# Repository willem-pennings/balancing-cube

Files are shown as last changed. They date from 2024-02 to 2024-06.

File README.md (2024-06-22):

## Balancing cube

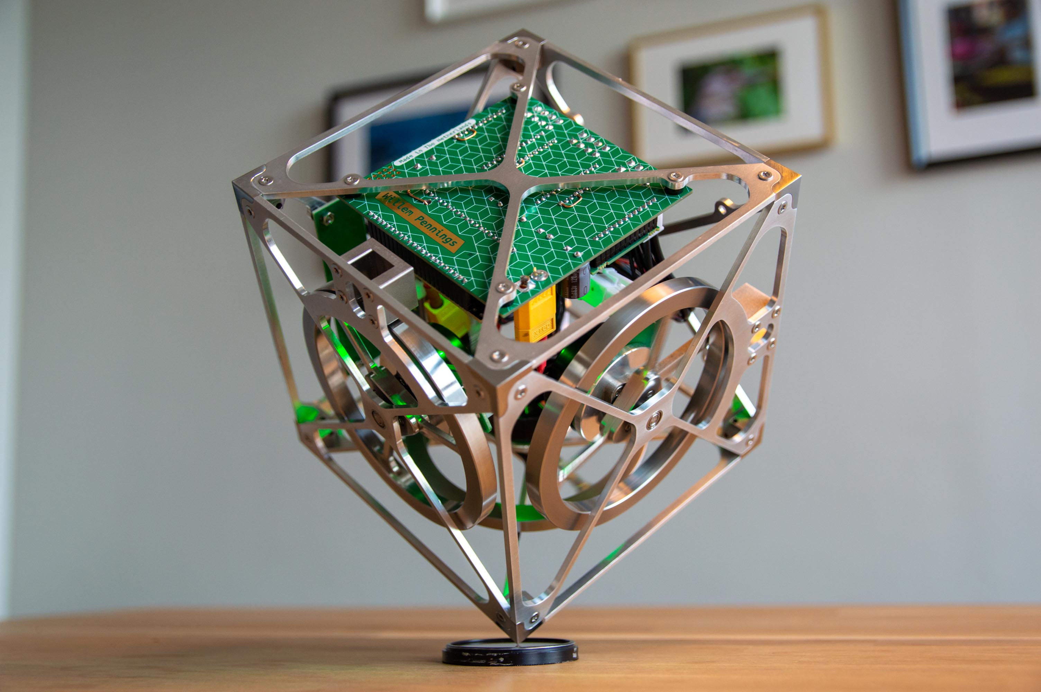
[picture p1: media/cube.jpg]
The cube balances on its corner using three integrated reaction wheels


This repository contains all design, documentation, configuration and other files related to the balancing cube that I have designed and built.
* Mechanical parts are designed in [Fusion 360](https://www.autodesk.com/products/fusion-360/personal).
* Circuit boards are designed in [KiCad 7](https://www.kicad.org/download/windows/).
* Code has been written using [Arduino IDE](https://docs.arduino.cc/software/ide-v2/tutorials/getting-started/ide-v2-downloading-and-installing/).
* Motor drivers are commissioned and tuned using [Escon Studio](https://www.maxongroup.nl/maxon/view/content/ESCON-Detailsite?isoCode=nl).
* Motors and motor controllers are available from [Maxon](https://www.maxongroup.com/maxon/view/content/index).
* Circuit boards and custom mechanical parts can be ordered from [PCBWay](https://www.pcbway.com/rapid-prototyping/), for example.

A YouTube video demonstrating the balancing cube is available [here](https://youtu.be/zGclFqkZBsk).

### Want to build one? Read this!

This repository should contain everything you need to order and/or build parts for this cube. Take into account the following:

* I replaced four of the eight 16AWG wires in each cable assembly by 22AWG wires since only four wires carry large currents. The others carry +5V and hall sensor signals. This reduces weight and makes the cables easier to handle, as well as reducing strain on the mating connectors. The motor connection is rather fragile and might break if stressed too much.
* The ESP32 board does not go into flashing mode automatically. I fixed this by adding a 10 uF capacitor between the enable and reset pin, as described [here](https://randomnerdtutorials.com/solved-failed-to-connect-to-esp32-timed-out-waiting-for-packet-header/).
* In my blog post, I describe some errors in the design of the motherboard. These have been resolved in the files that are available in this repository.
* For your own safety, I highly recommend taking precautions to reduce the risk of trapping fingers between the spinning flywheels. One option is to attach very thin (spring steel) discs to each wheel, which may be (laser)cut from larger sheets that are readily available. I do not have designs available for such safety devices yet.

### More information

More information about this project and my other projects is available on my [website](https://willempennings.nl/balancing-cube/).

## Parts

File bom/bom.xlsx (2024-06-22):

Quantity | Name | Designators | Part number | Supplier
3 | Aluminium Electrolytic Capacitors - Radial Leaded 120uF 63 Volts 20% | C1, C2, C3 | 647-UPM1J121MHD6TO | Mouser
1 | Aluminium Electrolytic Capacitors - Radial Leaded 50volts 470uF 18x15 20% 7.5LS | C4 | 647-UPJ1H471MHD6 | Mouser
1 | Aluminium Electrolytic Capacitors - Radial Leaded 25volts 220uF 10x12.5 '20% 5LS | C5 | 647-UPJ1E221MPD6 | Mouser
6 | Multilayer Ceramic Capacitors MLCC - SMD/SMT 50V 0.1uF X7R 0603 10% Flex AEC-Q200 | C6, C7, C8, C9, C10, C11 | 80-C0603X104K5R3316 | Mouser
2 | Multilayer Ceramic Capacitors MLCC - SMD/SMT 10V 10uF X5R 0603 20% | C12, C13 | 80-C0603C106M8PACTU | Mouser
3 | ESD Suppressors / TVS Diodes 33V 1000W UniDir TransZorb 5% Tol | D1, D2, D3 | 78-SMBJ33A | Mouser
1 | Schottky Diodes & Rectifiers 40V 3A SCHOTTKY RECTIF | D4 | 863-NRVBSS34FA | Mouser
3 | ESD Suppressors / TVS Diodes 3.3V Bidirectional | D5, D6, D7 | 652-CDDFN2-T3.3B | Mouser
3 | Surface Mount Fuses 260C 4A SMF NANO CLIP VFA | F1, F2, F3 | 576-0157004.DR | Mouser
4 | XT60 connector female |  | 474-PRT-10474 | Mouser
4 | XT60 connector male | J1 | 474-PRT-10474 | Mouser
3 | Headers & Wire Housings 8 CKT VERT HEADER | J2, J3, J4 | 538-39-28-1083 | Mouser
3 | Rectangular Cable Assemblies MINIFIT JR DR R-R 8CKT 150MM Sn |  | 538-215325-1081 | Mouser
1 | Headers & Wire Housings Classic PCB Header Strips, 0.100" pitch | J5 | 200-TSW10607LT | Mouser
1 | Power Inductors - SMD Ind,11x10x5.1mm,68uH+/-20%,3.5A,shd | L1 | 652-SRP1050WA-680M | Mouser
2 | MOSFET 50V, 0.26A, Single N-Channel Power MOSFET | Q1, Q2 | 821-BSS138 | Mouser
4 | Thick Film Resistors - SMD 10K OHM 5% | R1, R2, R3, R4 | 71-RCA060310K0JNEA | Mouser
1 | WiFi Development Tools - 802.11 ESP32-S3 Gen-Purpose Dev Bd, ESP32-S3-WROOM-1 | U4 | 356-EP32S3DVKTC1N8R8 | Mouser
1 | Switching Voltage Regulators 150 KHZ 3A STEP-DOWN VLTG REG | U5 | 926-LM2596SX-5.0NOPB | Mouser
1 | LDO Voltage Regulators High Vin, Low Iq Regulator | U6 | 998-MIC5225-1.8YM5TR | Mouser
1 | IMUs - Inertial Measurement Units World's Lowest Power 9-Axis MEMS MotionTracking | U7 | 410-ICM-20948 | Mouser
7 | Headers & Wire Housings |  | 801-87-011-10-005101 | Mouser
3 | Headers & Wire Housings |  | 801-87-013-10-005101 | Mouser
2 | Slide Switches Slide DPST | SW1, SW2 | 611-L201011MS02Q | Mouser
3 | EC 45 flat ∅42.8 mm, brushless, 60 W, with Hall sensors | Open rotor |  | 591477 | Maxon
3 | ESCON Module 24/2, 4-Q servo controller for DC/EC motors, 2/6 A, 10-24 VDC |  | 466023 | Maxon
3 | Machined part: motor frame (aluminium 6061)
3 | Machined part: regular frame (aluminium 6061)
3 | Machined part: bridge (stainless steel 304)
3 | Machined part: hub (stainless steel 304)
3 | Machined part: wheel (stainless steel 304)
4 | Machined part: Cornerstone A/CW (stainless steel 304)
4 | Machined part: Cornerstone B/CCW (stainless steel 304)
1 | Tattu Funfly Series 1300mAh 22.2V 100C 6S1P LiPo
1 | Custom PCB: cube-motherboard (4-layer ENIG)
1 | Custom PCB: cube-batteryboard (2-layer HASL)
9 | Machine screw M3x6 countersunk (motor - bridge)
8 | Machine screw M3x10 countersunk (frame - batteryboard, frame - motherboard)
8 | Nut M3
8 | Nylon spacer black ID 3.2 mm OD 7 mm
9 | Set screw hex M3x4 (hub - motor)
9 | Machine screw M2x6 countersunk (wheel - hub)
36 | Machine screw M3x8 countersunk (cornerstone - frame, frame - bridge)
3 | Radial ball bearing, 4 mm x 9 mm x 4 mm (bore diameter x outer diameter x width) |  | 638-4-ZZ-SKF

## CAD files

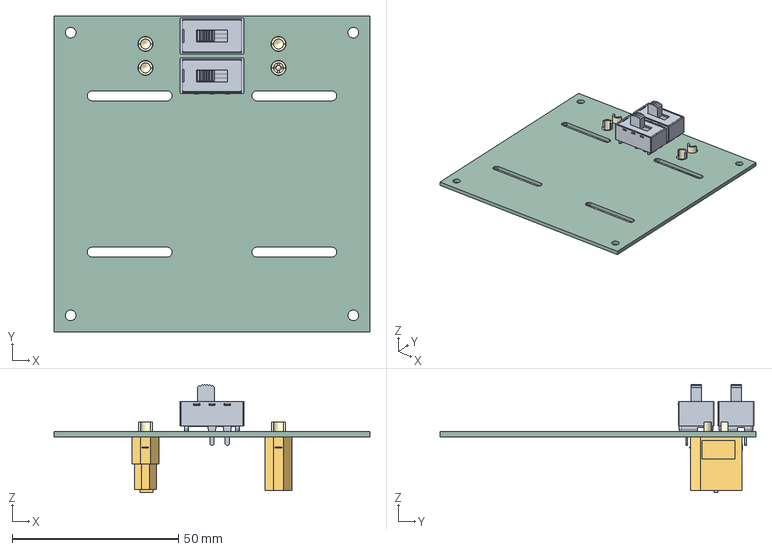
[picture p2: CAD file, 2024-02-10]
electronics/cube-batteryboard/cube-batteryboard.step
95.0 x 95.0 x 32.6 mm
Cubli batteryboard PCB

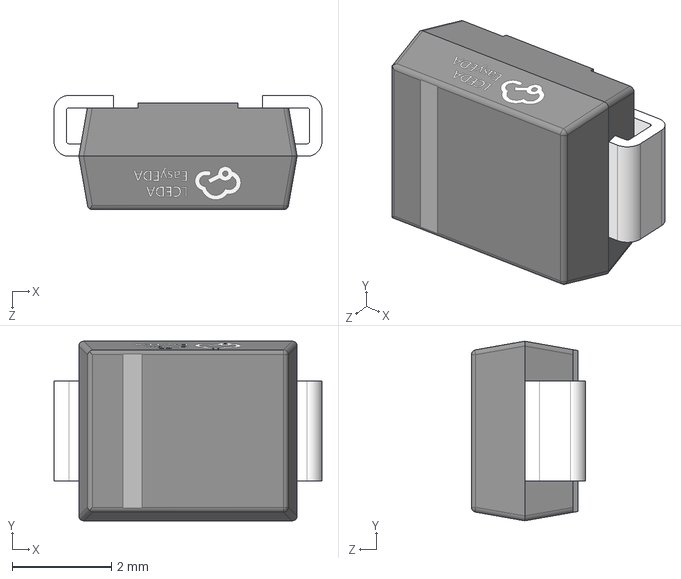
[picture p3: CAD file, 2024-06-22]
electronics/cube-motherboard/3d models/SMB_L4.4-W3.6-LS5.4-RD.step
5.40 x 3.62 x 2.30 mm

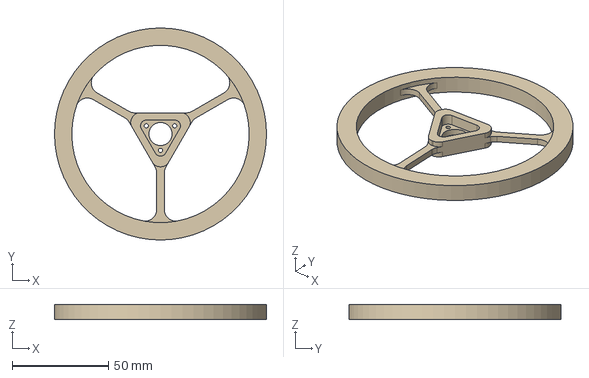
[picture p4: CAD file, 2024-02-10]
mechanical/models/wheel.step
110.0 x 110.0 x 8.00 mm

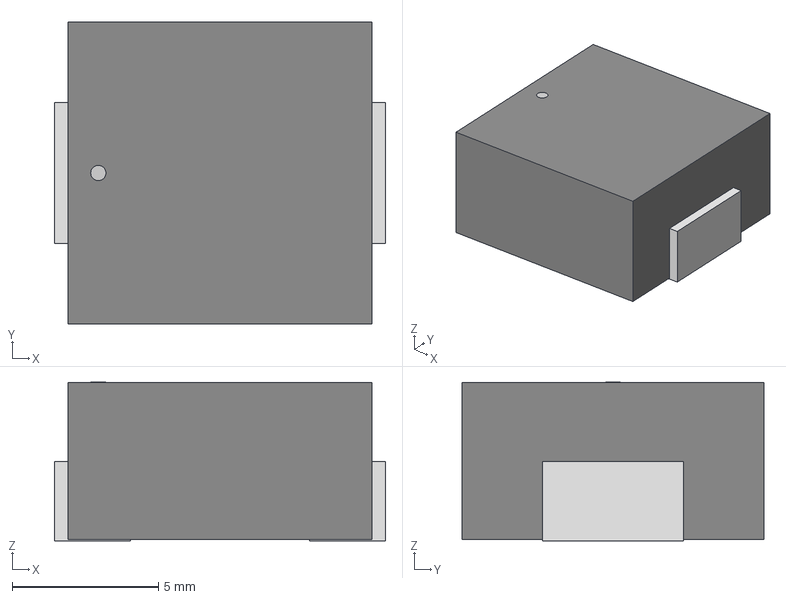
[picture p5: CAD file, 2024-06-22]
electronics/cube-motherboard/3d models/IND_SRP1050_BRN.step
11.3 x 10.3 x 5.41 mm

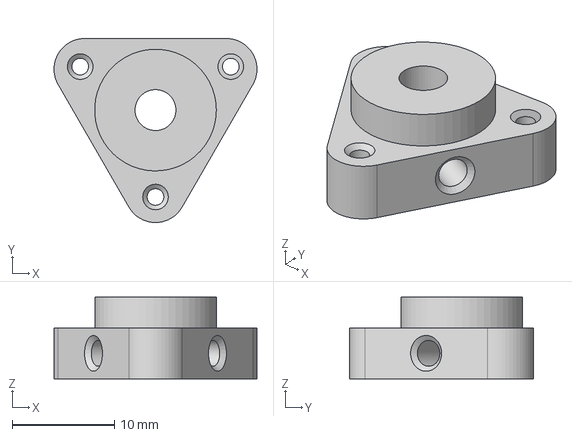
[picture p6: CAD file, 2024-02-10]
mechanical/models/hub.step
19.9 x 18.0 x 8.00 mm

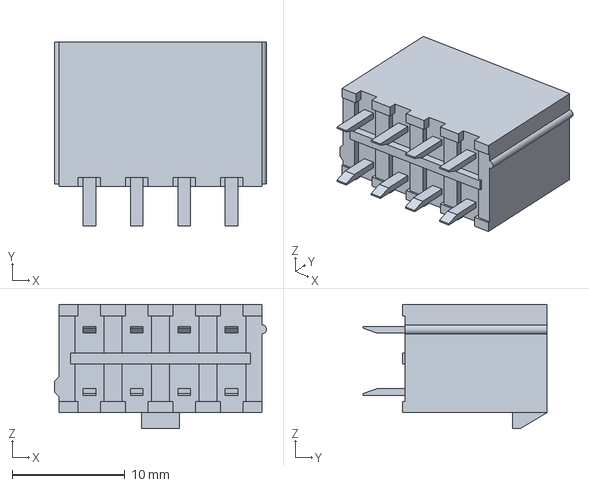
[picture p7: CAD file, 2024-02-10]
electronics/cube-motherboard/3d models/Molex 39281083.stp
18.8 x 16.3 x 11.0 mm

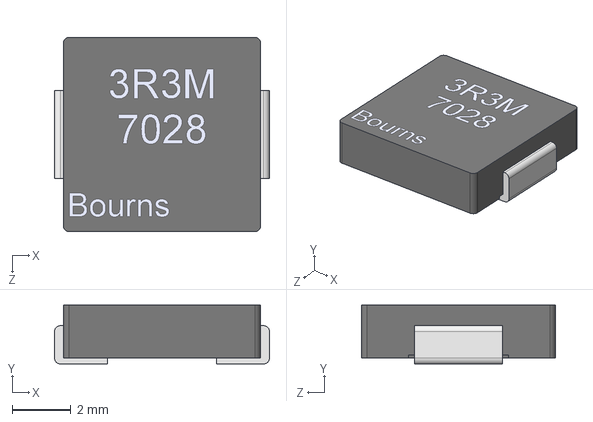
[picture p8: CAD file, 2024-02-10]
electronics/cube-motherboard/3d models/SRP7028A-3R3M.STEP
7.30 x 2.00 x 6.60 mm

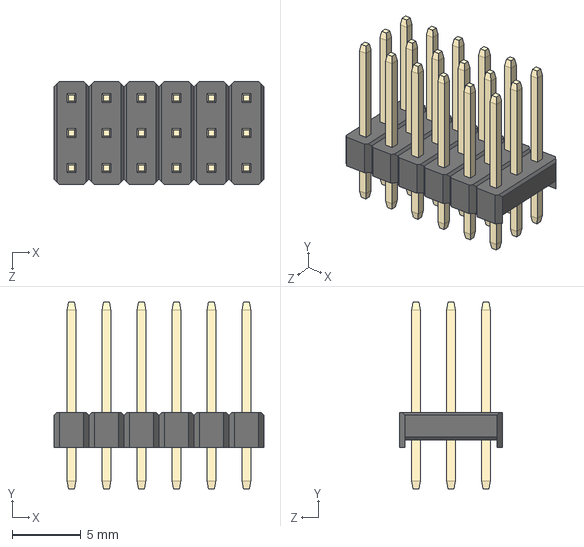
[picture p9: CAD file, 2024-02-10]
electronics/cube-motherboard/3d models/3x6 Male Pin Header.STEP
15.2 x 13.5 x 7.50 mm

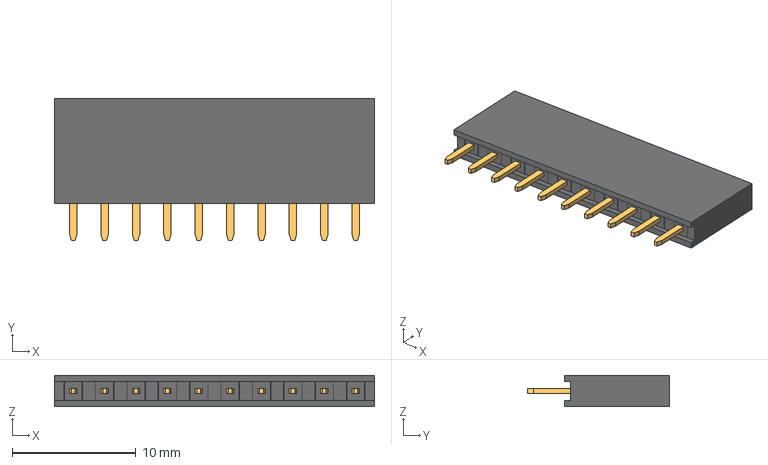
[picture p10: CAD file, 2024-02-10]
electronics/cube-motherboard/3d models/zl262-10s_p2-54_l25-9_w2-5_h8-5.stp
25.9 x 11.5 x 2.54 mm

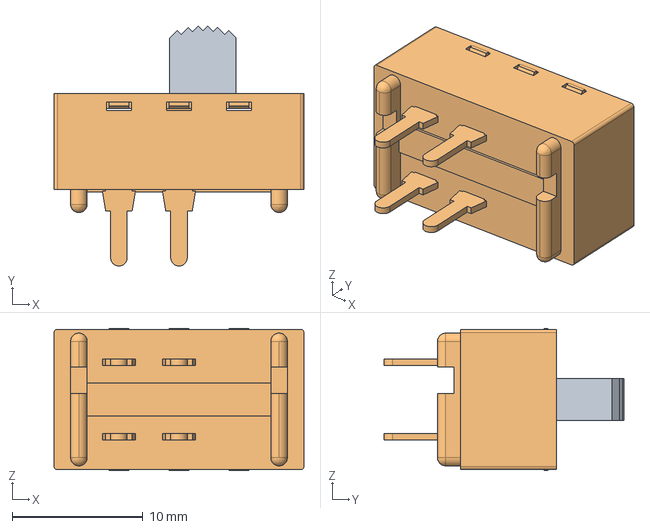
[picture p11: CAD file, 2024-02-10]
electronics/cube-batteryboard/3d models/L201011MS02Q.stp
19.1 x 18.4 x 10.9 mm

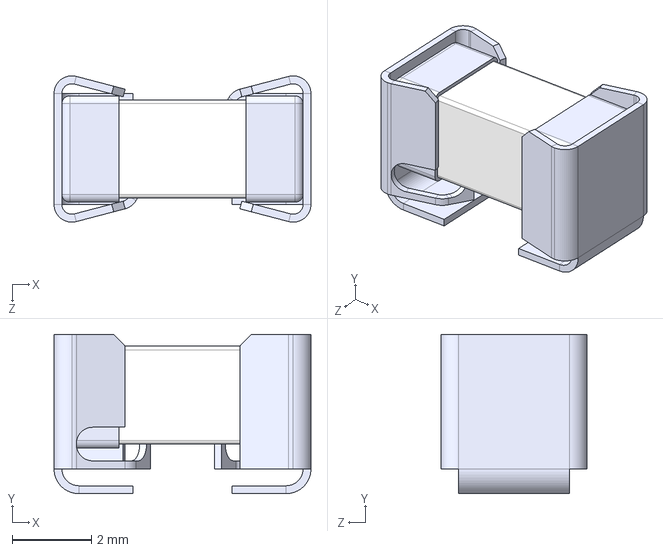
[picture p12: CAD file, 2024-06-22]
electronics/cube-motherboard/3d models/0157004.DRT.STEP
6.50 x 4.03 x 3.70 mm

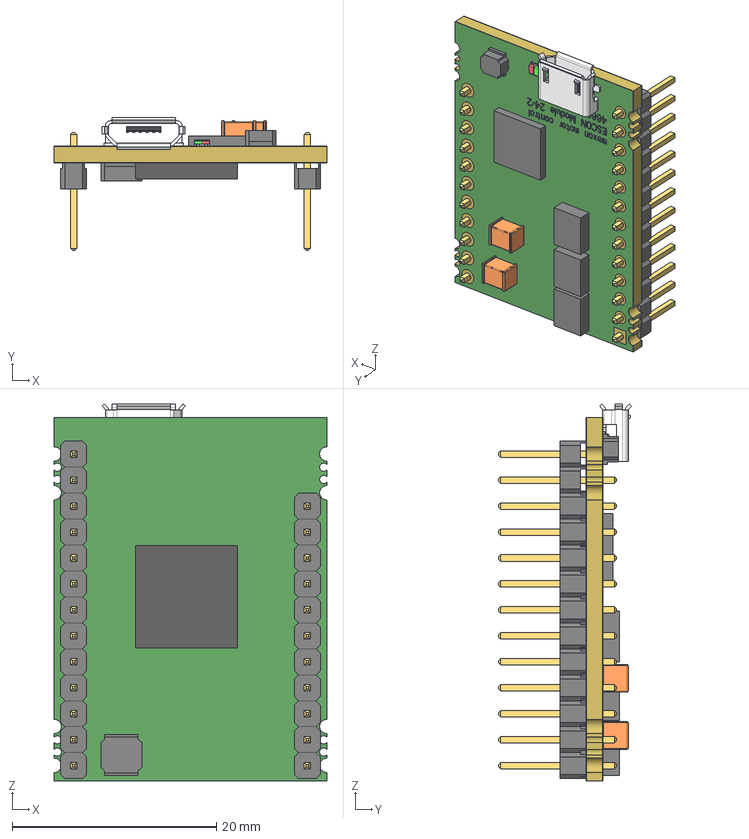
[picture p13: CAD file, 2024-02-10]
electronics/cube-motherboard/3d models/466023_escon_module_24-2.stp
26.7 x 13.0 x 36.9 mm
ESCON_24-2_MODULE_PCB
CAP_C3225 x 2
USB_MICRO
IC_7X7X1
DROSSEL_4X4X1-8
IC_LQFP64-10X10
ESCON_24-2_MODULE_PCB_SI-T
ESCON_24-2_MODULE_PCB_SI-B
STIFTLEISTE_1X1_K x 24
STIFTLEISTE_STIFT x 24
LED-0606_DUAL_SOCKEL
LED-0606-DUAL_GRUEN
LED-0606-DUAL_ROT
IC_SO-08 x 3
DROSSEL_3X3X1-5

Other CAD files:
mechanical/models/bridge.f3d
mechanical/models/cornerstone-a.f3d
mechanical/models/cornerstone-b.f3d
mechanical/models/frame-motor.f3d
mechanical/models/frame-regular.f3d
mechanical/models/hub.f3d
mechanical/models/mount-brake.f3d
mechanical/models/wheel.f3d

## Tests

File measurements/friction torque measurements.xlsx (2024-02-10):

Current (A) | Torque (Nm) | Speed (rpm) | Speed (rad/s) | Remark
0.050 | 0.00180 | 0.00 | 0.00
0.100 | 0.00360 | 0.00 | 0.00
0.110 | 0.00396 | 0.00 | 0.00
0.120 | 0.00432 | 0.00 | 0.00
0.130 | 0.00468 | 0.00 | 0.00
0.140 | 0.00504 | 1029.00 | 107.76 | Static friction overcome
0.150 | 0.00540 | 1227.00 | 128.49
0.160 | 0.00576 | 1476.00 | 154.57
0.170 | 0.00612 | 1687.00 | 176.66
0.180 | 0.00648 | 1890.00 | 197.92
0.190 | 0.00684 | 2130.00 | 223.05
0.200 | 0.00720 | 2380.00 | 249.23
0.210 | 0.00756 | 2640.00 | 276.46
0.220 | 0.00792 | 2852.00 | 298.66
0.230 | 0.00828 | 3109.00 | 325.57
0.240 | 0.00864 | 3349.00 | 350.71
0.250 | 0.00900 | 3597.00 | 376.68
0.260 | 0.00936 | 3819.00 | 399.92
0.270 | 0.00972 | 4032.00 | 422.23
0.280 | 0.01008 | 4260.00 | 446.11
0.290 | 0.01044 | 4475.00 | 468.62
0.300 | 0.01080 | 4639.00 | 485.79
0.310 | 0.01116 | 4896.00 | 512.71
0.320 | 0.01152 | 5102.00 | 534.28
0.330 | 0.01188 | 5345.00 | 559.73
0.340 | 0.01224 | 5618.00 | 588.32
0.350 | 0.01260 | 5830.00 | 610.52
0.360 | 0.01296 | 5890.00 | 616.80 | Output voltage saturation
0.140 | 0.00504 | 1069.00 | 111.95 | Back towards zero
0.130 | 0.00468 | 862.00 | 90.27
0.120 | 0.00432 | 650.00 | 68.07
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

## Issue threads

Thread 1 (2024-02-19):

Include parts list?

x46085, 2024-02-19:
Hello!

I've set about trying to build this, and ordered all the parts listed in the Article and Readme / in repo.

I've ordered:
- motors
- motor controllers

I'm currently missing:
- the exact countersunk screws & count
- the capacitors by type and count
- the other transistors / parts seen on the PCBs
- the exact small radial ball bearing used
- the exact battery used (useful for dimensions even if I get a different one)

A picture of the PCB without the controllers and ESP32 in place would be helpful, especially to see the IMU placement and make sure I have it correct.

Thank you for creating this project! It's enjoyable and inspiring to build.

willem-pennings, 2024-02-21:
I suppose you haven't found the BOM yet. It is available in the repository. I did notice that I forgot to add the ball bearings. I have added them now.

x46085, 2024-02-21:
Awesome, thanks!

Closed 2024-02-21.

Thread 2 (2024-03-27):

Clarification Opportunities

x46085, 2024-03-27:
Hello!

First off I want to reiterate how amazing your work here has been to replicate. The design work of the CAD models and electronics are truly world class; the pieces first together beautifully and things are relatively easy to follow.

Some discoveries I've had while building this:

1. Unclear on Routing Error / Bodge Wire reference: in the website you have a picture showing a mistake made on the routing for the motor controllers and how you corrected it with a bodge wire bridge. It's unclear to me if I need to replicate this, or if you corrected the routing in the final PCB design. Could you help explicitly clarify either way so I know what I should do?

2. Well-lit / High Res Picture to help with placement: I've struggled to determine if all my placed components are in the correct orientation. I found and followed the schematic in most cases, but I would find it extremely useful to have a well-lit, close-up top-down picture of the board (before placing the dev board). There is one dark picture on the website where I could see my fuses were backward and fix it, and I think the TVS Diodes have the cathode / grey stripe to the right, but I can't quite see.

3. I noticed there is no description of the steps used to flash the dev board. While I'm capable of bumbling through basic Arduino setup and the trial and error process of installing Expressif plug-ins until I find the right things to target this board, and figuring out which connection to plug into and what port this resolves to in Arduino, having any sort of steps laid out as a template / what worked before would greatly assist me in getting it right sooner and more easily.

4. I ordered everything in the BOM, and I seem to be missing the battery cable from the power board to the motherboard. Could you provide the reference to that / add to the BOM?

5. I don't seem to see where I can understand which motor controller board connects to which motor. I'm studying the pictures to try and see, but it's not very clear.

Again this is a beautiful work of art! Thank you for building & sharing.

willem-pennings, 2024-04-01:
Hi! Thanks for the remarks. That is good to hear. Please share pictures of your build with us, either here or by sending me an e-mail through my website. That would be nice.

Regarding your questions:

1. The hardware errata have been fixed in the files that are available. There is one very minor issue which I have not fixed since it can be easily corrected in software: the pin that I had intended to use for motor speed feedback on motor driver 3 is connected to ADC2 on the ESP32. This ADC does not seem to work well when WiFi is enabled on the ESP32. However, the second analog output is connected to ADC1, hence I just modified the configuration file to swap the signals for the third driver. This works fine. The other pin is connected for motor current feedback purposes, but this signal is not needed and therefore unused.
2. I'll try to add some pictures later. For 99% of your issues, inspecting the schematic and using the 3D viewer in KiCad will answer all your questions. However, I noticed that the 3D viewer actually displays the TVS diodes incorrectly. The schematic also shows a bidirectional TVS diode whereas in reality it's just a undirectional one. I'll try to fix that too.
3. I'm assuming a certain level of competence. Arduino projects are already very accessible and I know that there are specific issues that one might run into when flashing ESP32 boards. However, I'm not going to cover them here since many tutorials are available concerning these matters.
4. The battery cable is a custom job. It uses XT60 connectors. You'll have to build it yourself or order something similar (there should be many options available). I recommend using AWG16 wire. It's about 150 mm long, but again, the required length depends on how you want to route it exactly.
5. This doesn't really matter since you can just re-assign each of the x, y and z axes in software by modifying `pins.h`. Do what works well for you. In my case, drivers 1, 2 and 3 are connected to the motors that control the y, z, and x axes, respectively.

Hope this helps. I'll keep the issue open until I add the pictures and fix diode polarity issue in the KiCad project.

x46085, 2024-04-01:
For sure! it's coming together:
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
and:
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

The second is me trying to program the motors. Did you program like this directly via this custom motherboard? or did you use Maxon's official board first? Still working through trying to get it working.

Just to clarify, I should or shouldn't have these bridges?:
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

willem-pennings, 2024-04-02:
Thanks! You can remove the bodge wires that you added to the motherboard. Looks like you've got the polarity of the TVS diodes right, the band should be pointing towards the corresponding fuse.

I have added some notes and tips to the main readme file which you'll want to check out!

x46085, 2024-04-02:
Indeed! I think these new comments reveal the missing piece that was preventing me from commissioning the motor controllers properly. I've got the official Maxon motherboard as well as the referenced tool ordered now. Thanks for the additions! Will post my progress (or email you if you prefer) once I get them.

Manny7115, 2024-04-24:
> Indeed! I think these new comments reveal the missing piece that was preventing me from commissioning the motor controllers properly. I've got the official Maxon motherboard as well as the referenced tool ordered now. Thanks for the additions! Will post my progress (or email you if you prefer) once I get them.

Have you been able to get your cube up and running?

If so, what steps did you take to calibrate the gryo and accelerometer?

I have a built cube, but cant seem to get it to stand on any edge. Currently the cube will only enable the motor controllers if it's placed on a specific edge with the wheels towards the top and not towards the bottom like in the video.

As a side note, I had to change some of the pinouts in the pins.h based on the schematic routing. Additionally the battery board schematic is missing the GND connection from the OUT connector to the GND plane, fix this before you send the board to be produced.

willem-pennings, 2024-05-29:
> Have you been able to get your cube up and running?
>
> If so, what steps did you take to calibrate the gryo and accelerometer?

Did you use the script that I provide? It gives some instructions on how to calibrate the gyro and accelerometer. You can verify whether your work was correct by logging the output of the AttitudeEstimator while placing the cube in certain orientations and/or rotating it about the various axes.

Manny7115, 2024-05-29:
I did use the calibration program and was able to configure the gyro but was a little unclear on how to calibrate the accelerometer or what gains to set to 0 for calibration. I believe my calibration values for the accel are correct since I am getting around 9.8 for the "Calibrated: Acc:" values on the different orientations and 1 for the G-value logging that I added.

What kind of values or ranges should I be looking for to determine if the main cube software is working as intended for the AttitudeEstimator?

Currently I have not been able to get the cube to balance on a corner, I have tried adjusting the PD gains of the main controller and of the wheels (I assume that Kpw and Kdw are the gains for the wheels). However with a little tweaking I have been able to get the edge balancing to work for a while but it seems that something is not entirely correct since the Phi value slowly creeps up and the qe1 and qe3 are increasing over time even though the wheels for those axis are not moving. This could all be related to the accelerometer or gyro since the signs of some of the gains were different than what you had.

cumhuronat, 2024-05-31:
I'm still confused about the TVS diodes. Both the schematics and the BOM list bidirectional diodes. The part number on the BOM, CDDFN2-T3.3B, is also bidirectional. If these diodes should be unidirectional, what would be the correct part number?

cumhuronat, 2024-06-01:
Also the [hardware reference of escon module](https://www.maxongroup.com/medias/sys_master/root/8834400092190/466023-ESCON-Module-24-2-Hardware-Reference-En.pdf) 24/2 suggests using CDDFN2-T3.3LC which is the predecessor of CDDFN2-T3.3B both of which are bidirectional.

cumhuronat, 2024-06-01:
Never mind, I just understood that you were talking about the diodes on the supply voltage :) Thank you so much for open sourcing this btw.

willem-pennings, 2024-06-29:
Considering the various design and documentation improvements that have been made since this issue was opened (also the contribution by Cumhur), I will now close this issue.

Closed 2024-06-29.

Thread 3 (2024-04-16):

Batteryboard design

Manny7115, 2024-04-16:
The schematic for the battery board has pin 1 on the OUT connector floating, I believe this is an error and they should be tied together to pin 1 of the IN connector.

Also based on the switch position the power flows opposite of the indicated ON or OFF labels. I have switched the labels and added pin 1 on the OUT connector to the GND plane on my own board.

willem-pennings, 2024-05-29:
Thank you for the remark. You are completely right! I must have messed this up between ordering the boards and adding them to this repository, because my boards do not have this issue. I have fixed the mistake now.

Closed 2024-05-29.

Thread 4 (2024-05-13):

fix github About

AndreiCherniaev, 2024-05-13:
I suggest to add tags:

robots
pid
pid-controller

willem-pennings, 2024-05-29:
I don't think tags related to PID control are suitable since the controller does not implement a PID controller. Thanks for the suggestion though.

Closed 2024-05-29.

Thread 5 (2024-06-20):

Overcurrent Error on Escon Controller

cumhuronat, 2024-06-20:
I keep getting Overcurrent Error randomly in a few seconds after the cube starts balancing and it causes the cube to fall. The error appears randomly in one of the 3 escon controllers. The error is both visible in the escon studio and with the status led (2 red blinks). I tried regulation tuning as well but it didn't help. Any ideas what might be the problem?
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

cumhuronat, 2024-06-20:
Thanks for sharing your pid values, will try them and let you know the result. Thanks again for making this opensource!

willem-pennings, 2024-06-20:
Thanks, I'm curious to know if this gives better results. I just noticed that the gains in my configuration files are wrong so I updated them with the values posted above. It probably explains your issue..!

cumhuronat, 2024-06-20:
It works like a charm now! Thank you
https://github.com/willem-pennings/balancing-cube/assets/529671/bb86d19a-39b8-46b5-92c9-854b028f8558

willem-pennings, 2024-06-20:
Excellent, congratulations!

Closed 2024-06-20.

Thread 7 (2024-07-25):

Clarifying Questions

Manny7115, 2024-07-25:
Thanks for updating the files and clarifying a few points, this has helped me get closer to a working cube. I have a few questions about axis mapping and calibration.

1. In the ICM20948.cpp file, why is it necessary to swap the axis? This to me seems as if its driving the wrong motor (y-axis) when I am trying to balance on the Y-axis...shouldn't the z-axis motor be one the driving?

2. How are you assigning the motors to the axis? does M1=x-axis, M2=y-axis and M3=z-axis?
2.1. With the motherboard flat on the table, the motor directly above it should be the z-axis and the motor closest to the yellow power connector should be the x-axis correct?

3. Calibrating the gyro is pretty straight forward, the offsets are initially set to 0 while the program is running the active gyro readings shown in the serial monitor are used as the new offset values. Proper calibration of the gyro should result in values close to 0 when the cube is on the table.

4. Calibrating the accelerometer is where things start to not make sense. If I want to calibrate the Z-axis readings do I set b_acc_z = 0 and f_acc_z = 1 while having the motherboard flat on the table?
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
I then invert the motherboard and take another reading of the Z-axis.
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
With both readings I can now calculate the gain and the offset for the axis?
4.1. Or is the offset for all of the axis simply determined when the axis are placed in a 0g field while the gain is determined by the large +/-16xxx readings?

willem-pennings, 2024-07-27:
1. The axes are swapped in the `ICM20948.cpp` file to align the coordinate system of the IMU with the coordinate system that the controller expects. Definitions are according to those shown in [this paper](https://arxiv.org/pdf/2009.14626) (Figure 2). If you look closely at how the IMU is mounted, how its reference frame is defined, and how that of the cube is defined, you'll notice that the X axes are already aligned, whereas the cube's Z axis is the IMU's y axis, and vice versa. This is why they are swapped.
2. The mapping of motors to axes is determined either by your pin definitions in `pins.h` or by the way you physically connect your motors to the motherboard. In the end, you should arrange both the wires and file such that motor 1 drives the X axis, motor 2 drives the Y axis, and motor 3 drives the Z axis. Regarding orientations, you can again refer to the paper that I linked.
3. Yes, and this gyro calibration step is done again every time the cube is powered on, so this step is not strictly necessary but good practice in my opinion.
4. The calibration procedure is described in a lot of detail in the application note that I link in my calibration program. You measure two points per axis, note down the raw values, do the offset and gain calculations (Eqns. 17 and 18), and then you feed the results back into the script to verify that you did it right. It doesn't matter what you set the `b` and `f` values to, because you don't use them during the actual calibration process. They're only used to calculate calibrated values after you do the procedure. Since you seem to be getting values of `16527` and `-16359` (your screenshot), your `b` is `84` and your `f` is `1676` for the Z axis. Plug in these values for the Z axis, and you'll see that the calibrated output returns `9.81` when you put the cube in the one Z orientation, and `-9.81` when you put it upside down with respect to the previous orientation.

Manny7115, 2024-07-29:
I appreciate you answering my questions and providing some pointers. I have been able to successfully calibrate the cube and get it to balance reliably on the X&Y edge. Balancing on the corner still seems a little off to me since all wheels ramp up to full speed as soon as the cube is moved into the starting position. This might means that I need to adjust the gains a bit to get the cube balancing on a corner.

willem-pennings, 2024-07-29:
It could also be an issue with your equilibrium point offset ‘phi_e’. Try adjusting that: for example try setting it to -3 deg and +3 deg and see if that helps.

Manny7115, 2024-07-30:
I actually was able to get the cube to balance on a corner for a couple of minutes before the limit error was triggered. To have the cube react normally I simply changed the wiring between M2 and M3 basically I swapped the Z-axis and Y-axis. I left the pinout in the pins.h file the same as what is shown in the latest file on the github. This to me indicates that the wiring is finally correct and that adjusting the PD gains is all that is left.

Just for my reference when you say xyz axis, is this based on the IMU or the cube itself? If I am understanding the linked paper correctly then the axis should be mapped as such and thus the wiring to the controllers are M1=X-axis, M2=Z-axis and M3=Y-axis with reference to the IMU.
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

liy012345, 2024-08-07:
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

Thanks, with your guidance, my cube is stable and steady, but I found that it can only balance for ten minutes or so (as the trajectory increases, the speed of the wheel slowly gets faster and then exceeds the limit value of the safety control, the red and green light flashes and shrinks alternately), is there a good solution for this problem?

willem-pennings, 2024-08-07:
> I actually was able to get the cube to balance on a corner for a couple of minutes before the limit error was triggered. To have the cube react normally I simply changed the wiring between M2 and M3 basically I swapped the Z-axis and Y-axis. I left the pinout in the pins.h file the same as what is shown in the latest file on the github. This to me indicates that the wiring is finally correct and that adjusting the PD gains is all that is left.
>
> Just for my reference when you say xyz axis, is this based on the IMU or the cube itself? If I am understanding the linked paper correctly then the axis should be mapped as such and thus the wiring to the controllers are M1=X-axis, M2=Z-axis and M3=Y-axis with reference to the IMU. ![image](https://private-user-images.githubusercontent.com/167252124/353275551-8d4816a3-e51e-48b4-b41c-86942cb5dd9c.png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)

Hello, I am always considering cube reference frame when I am talking about axes. So yes, the cube and IMU X axis coincide, whereas the IMU Y and Z axes are swapped when converting to the cube reference frame. This is also reflected in the piece of code which you referenced before. There are no other reference frame conversions from the top of my head, except for the one that corrects the sign of the wheel direction.

willem-pennings, 2024-08-07:
Seems like the original issue has been solved so I will close this issue now.

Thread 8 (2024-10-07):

Recent updates?

mhkeller, 2024-10-07:
I noticed that in [this comment](https://github.com/willem-pennings/balancing-cube/issues/7#issuecomment-2274198622), you mentioned that you were working on a large update with some new features – which I'm hoping includes the braking ability you mention in your original blog post that would allow it to jump up to its edge and its point. If you have a sense of your timeline in pushing this update out, please let me know. I'm scoping out starting this as a project but would prefer to wait until the new info is there. Thanks again for putting this together and for making it so accessible.

willem-pennings, 2024-10-11:
I still plan to update the controller software at some point to resolve some issues and add a few new features. I don't foresee hardware updates currently. The jumping feature is quite advanced and I haven't decided on a concept yet, so I personally wouldn't wait for it if you're keen on building this. While the cube design already has some mounting points for components related to the jump up feature, I can't guarantee that the design will be backwards compatible with the current cube design.

mhkeller, 2024-10-15:
Thanks for the update. I'm in no rush and have a few few projects still on my plate!

liy012345, 2025-05-06:
Hi，earlier I noticed that the cube could only time balance for about 10-20 minutes, and I'm wondering what causes this, zero drift in the gyroscope, or steady state error in the PD controller? Is there any way to solve the problem of the cube balancing time length, (can I theoretically turn it until the battery is dead? Or detecting how many volts the LiPo battery is below to turn off the output;)

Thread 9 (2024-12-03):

Firmware settings

hexa1992, 2024-12-03:
I am currently building the cube and have a few questions about the firmware.
At the moment, the cube does not balance on one corner. Therefore, I wanted to first try balancing on a corner. For this, I made the following changes:

In the **parameters.h**, I deactivated
```
// Quaternion reference (Cubli sitting on on corner, corrected for center of mass misalignment)
//const float phi_e = 0 * pi / 180.0;
//const float qu0 =                    cos(phi_e / 2.0 + acos(sqrt(3.0) / 3.0) / 2.0);
//const float qu1 =  sqrt(2.0) / 2.0 * sin(phi_e / 2.0 + acos(sqrt(3.0) / 3.0) / 2.0);
//const float qu2 = -sqrt(2.0) / 2.0 * sin(phi_e / 2.0 + acos(sqrt(3.0) / 3.0) / 2.0);
//const float qu3 =  0.0;
```

and uncommented the following lines lines:
```
// Quaternion reference (Cubli sitting on x axis edge, corrected for center of mass misalignment)
 const float phi_e = -3.0 * pi / 180.0;
 const float qu0 = cos(phi_e / 2.0 - pi / 8.0);
 const float qu1 = cos(phi_e / 2.0 + 3.0 * pi / 8.0);
 const float qu2 = 0.0;
 const float qu3 = 0.0;
```

In the **cube-controller.ino**, I also commented out .
`//att_tra.generate();`

Despite the code changes, all three motors still turn on when I start the cube on its X-axis edge.

Do I need to change anything else?

On Willem Pennings' homepage, he explains in the comments that all motors must rotate counterclockwise. However, when I look at my motors from the outside, they are rotating clockwise. Is this a matter of perspective, or is it correct this way?
In the video, the wheels also rotate clockwise when viewed from the outside. Therefore, this statement is somewhat confusing.

willem-pennings, 2024-12-15:
These are indeed the correct changes to make the cube balance on a side instead of a corner. I hope the comments in the Arduino source file are mostly self-explanatory. I'll go ahead and close this one.

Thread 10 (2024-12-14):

Optional Switch for balancing modes

hexa1992, 2024-12-14:
I have developed a small circuit board that connects to the pin header of the servo motors. I would like to adjust the code so that, before powering on the cube, various settings can be configured using the switches.

In my opinion, the following settings would make sense:
	•	Selection of the balancing mode
	•	Activation of OTA update capability

Unfortunately, my programming skills are not sufficient to adapt the code accordingly.
I have already managed to successfully activate the corresponding code lines using **_if_** statements in the main program. However, this unfortunately does not work in the **_parameters.h_** file, as **_if_** statements are not possible there.

I would greatly appreciate a suggestion for a solution!
I’d be happy to upload the PCB layout here if you’re interested!
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

willem-pennings, 2024-12-15:
Hey,

Looks like a neat little board. You could try modifying the code as follows to make it work.

The references as defined in `parameters.h` are only used in `trajectory_attitude.cpp`. However, the orientation is set by uncommenting the desired one, so the controller only "knows" one reference at run time. In your case, you want to determine the orientation at runtime, so it makes more sense to build a generic `if` statement in `cube_controller.ino` which defines the orientation (one of three) based on a digital pin reading (more on that below). It could look something like this (pseudocode):

```
if (x edge mode) {
  qu0 = a;
  qu1 = b;
  qu2 = c;
  qu3 = d;
} else if (y edge mode) {
  qu0 = e;
  qu1 = f;
  qu2 = g;
  qu3 = h;
} else {
  // corner mode.
}

Considering that `controller_attitude.cpp` currently reads the orientation directly from the values as defined in `parameters.h`, which we do not want in your case, you could for example add a method to this class to set the reference orientation explicitly, like `set_reference()`, instead of copying the values from `parameters.h` in the constructor. You would then call this method using four arguments (the `qu` values as determined using the code above) in the `setup()` method in `cube_controller.ino`. The class is now ready for "dynamic" runtime reference selection.

To actually read the state of the DIP switches in your program, I would advise using `digitalRead()` (and `pinMode()`) in the `setup()` function in `cube_controller.ino`. Certain combinations of switches would result in certain balancing orientations, so you would put the output of the `digitalRead()` calls in the `if` block above.

If you want to change the orientation without resetting the microcontroller, you would not (only) read the DIP switches in the `setup()` function. but instead in a function which you call periodically, perhaps using a timer construction like I already do in the program to for example call the `controller()` function periodically.

I hope this helps. Do let us know whether you can get it to work.

hexa1992, 2024-12-16:
I gave the software another try. I was able to successfully modify the code lines in the `cube-controller.ino`. Unfortunately, I couldn't implement the changes involving the constants in `parameters.h`.

My code section works and has been tested by me. Depending on the switch position, you just need to adjust the corresponding block in `parameters.h`, and everything will work perfectly.

I made the following changes to `cube-controller.ino`:

I´ve added
```
#include <set> // Für Tracking bereits ausgegebener Nachrichten

// Globale Datenstruktur zum Speichern bereits ausgegebener Nachrichten
std::set<String> loggedMessages;

``` after line 27.
This is only needed for debugging purposes in the serial monitor.

I´ve added
```
  // Configure DIL-Switches as inputs
  pinMode(DILSW1, INPUT_PULLDOWN); // internal pulldown active

  // Mode selection
  modeselection();
``` after line 70.

I´ve added
```
// Logging-Funktion
void logMessage(const String &functionName, const String &message, const String &values = "")
{
  String fullMessage = "[" + functionName + "] " + message;
  if (values != "")
  {
    fullMessage += ": " + values;
  }

  // Prüfen, ob Nachricht bereits ausgegeben wurde
  if (loggedMessages.find(fullMessage) == loggedMessages.end())
  {
    Serial.println(fullMessage);
    loggedMessages.insert(fullMessage); // Nachricht speichern
  }
}
```  and
```
void modeselection()
{
  if (digitalRead(DILSW1) == 1)
  {
    MODE = 2; // balancing on corner
    logMessage("modeselection", "Mode selected", "Corner balancing activated");
  }
  else
  {
    MODE = 0;
    logMessage("modeselection", "Mode selected", "X side balancing activated");
  }
}
``` after line 129, where `void logMessage` is only needed for debugging purposes in the serial monitor.

I´ve changed `att_tra.generate();` in line 185 to
```
if (MODE == 2)
    {
      att_tra.generate();
      logMessage("controller", "generate() method", "activated");
    }
    else
    {
      logMessage("controller", "generate() method", "deactivated");
    }
```

In line 210 i´ve changed
```
// Apply torques to motors
  // When balancing on the x side, comment out motor 2 and 3. When balancing on the y side, comment out 1 and 3.
  motor1.set_torque(tau_1);
  motor2.set_torque(tau_2);
  motor3.set_torque(tau_3);
``` to
```
// Apply torques to motors
  // When balancing on the x side, comment out motor 2 and 3. When balancing on the y side, comment out 1 and 3.
  if (MODE == 0)
  {
    // Nur Motor 1 aktivieren
    motor1.set_torque(tau_1);
    logMessage("controller", "Motors activated", "Motor 1 only");
  }

  if (MODE == 1)
  {
    // Nur Motor 2 aktivieren
    motor2.set_torque(tau_2);
    logMessage("controller", "Motors activated", "Motor 2 only");
  }

  if (MODE == 2)
  {
    motor1.set_torque(tau_1);
    motor2.set_torque(tau_2);
    motor3.set_torque(tau_3);
    logMessage("controller", "Motors activated", "Motor 1, 2 & 3");
  }
```

also i added the following to `pins.h`:
```
// Variables for 6 DIL-Switch at Servo Inputs
const int DILSW1 = 1;
const int DILSW2 = 2;
const int DILSW3 = 42;
const int DILSW4 = 41;
const int DILSW5 = 40;
const int DILSW6 = 39;
```
When the switch DILSW1 is closed, MODE 2 is activated, and the cube balances on its corner. When the switch is open, MODE 0 is activated, and the cube balances on its X-axis.

If you now modify the corresponding part of the code in parameters.h, the change will work!

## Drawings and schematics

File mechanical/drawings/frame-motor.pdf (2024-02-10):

142 150

# 4x Ø7 x 90°

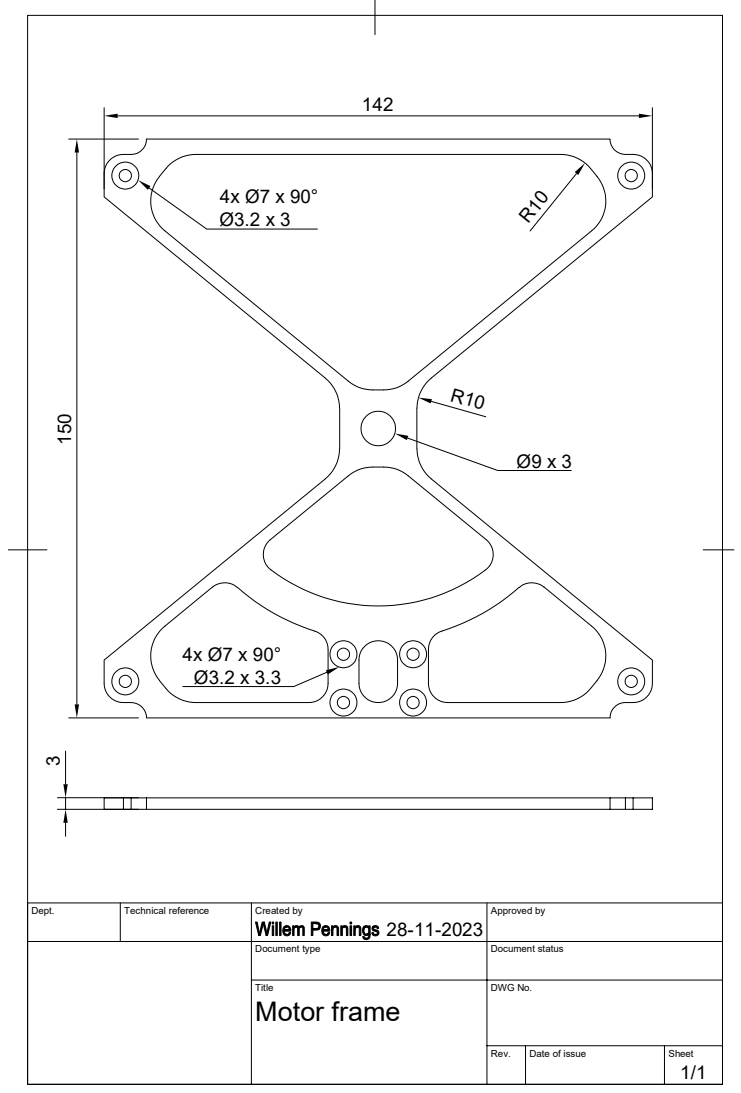
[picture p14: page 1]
Dept.; Technical reference; Created by; Approved by; Document type; Document status; Title; DWG No.; Rev.; Date of issue; Sheet; Motor frame; R¹⁰

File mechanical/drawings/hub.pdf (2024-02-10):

Ø11.9 ⁰
-.1

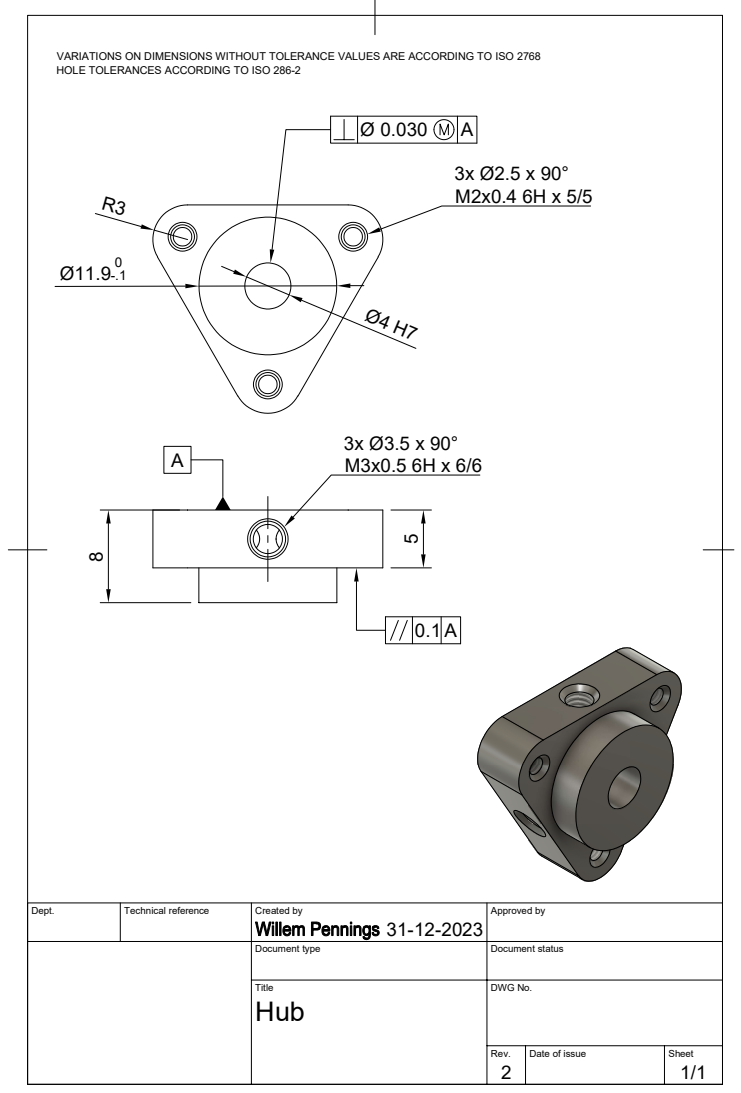
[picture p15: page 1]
Dept.; Technical reference; Created by; Approved by; Document type; Document status; Title; DWG No.; Rev.; Date of issue; Sheet; Hub

VARIATIONS ON DIMENSIONS WITHOUT TOLERANCE VALUES ARE ACCORDING TO ISO 2768
HOLE TOLERANCES ACCORDING TO ISO 286-2

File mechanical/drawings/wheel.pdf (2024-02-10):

A | Ø¹¹⁰ | A-A (1:1)

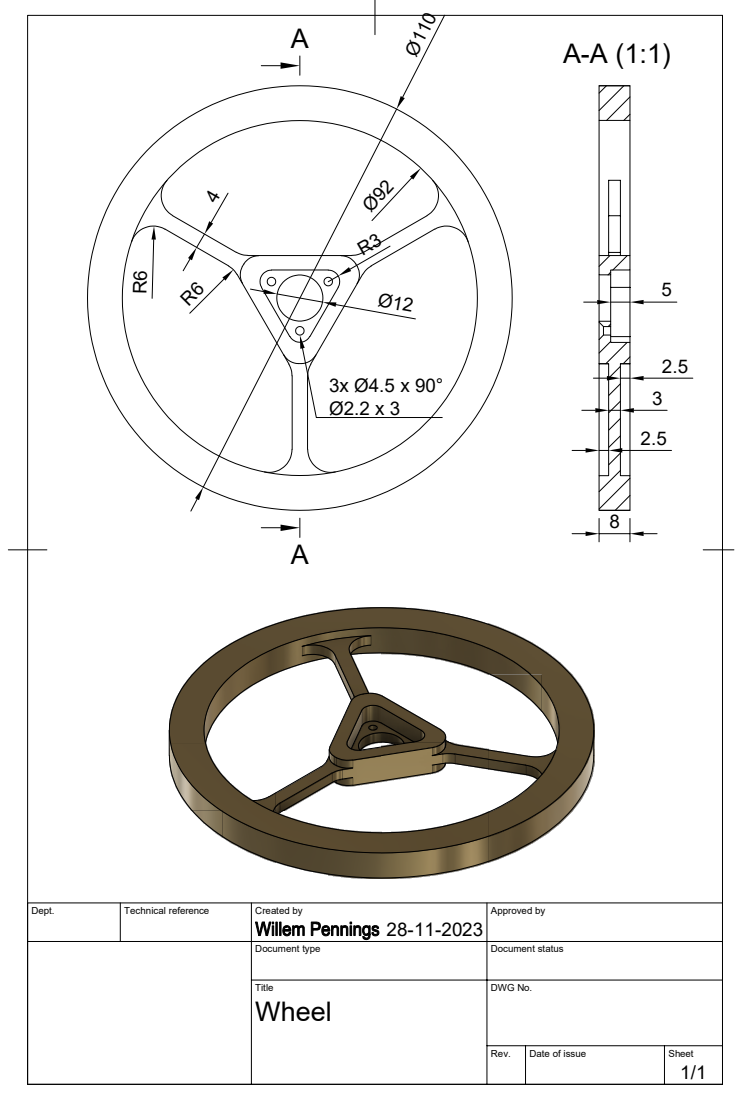
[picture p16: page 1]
Dept.; Technical reference; Created by; Approved by; Document type; Document status; Title; DWG No.; Rev.; Date of issue; Sheet; Wheel

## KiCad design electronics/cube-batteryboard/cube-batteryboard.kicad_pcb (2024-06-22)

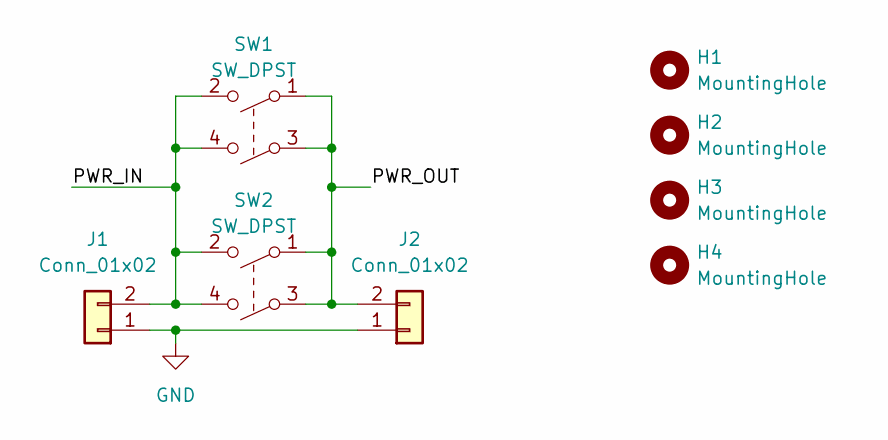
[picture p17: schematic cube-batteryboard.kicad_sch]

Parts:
H1, H2, H3, H4: MountingHole; MountingHole_3.2mm_M3_DIN965_Pad
J1: Conn_01x02; AMASS_XT60-M_1x02_P7.20mm_Vertical
J2: Conn_01x02; AMASS_XT60-F_1x02_P7.20mm_Vertical
SW1, SW2: SW_DPST; L201011MS02Q

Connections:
/PWR_IN: J1.2, SW1.2, SW1.4, SW2.2, SW2.4
/PWR_OUT: J2.2, SW1.1, SW1.3, SW2.1, SW2.3
GND: J1.1, J2.1

Board: 2 copper layers, 13 parts (9 on the bottom side), 3 nets, no tracks yet.

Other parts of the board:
kibuzzard-65634FCA: G***; kibuzzard-65634FCA
kibuzzard-656351C1: G***; kibuzzard-656351C1
kibuzzard-656351D2: G***; kibuzzard-656351D2
kibuzzard-656351E7: G***; kibuzzard-656351E7
kibuzzard-65635119: G***; kibuzzard-65635119

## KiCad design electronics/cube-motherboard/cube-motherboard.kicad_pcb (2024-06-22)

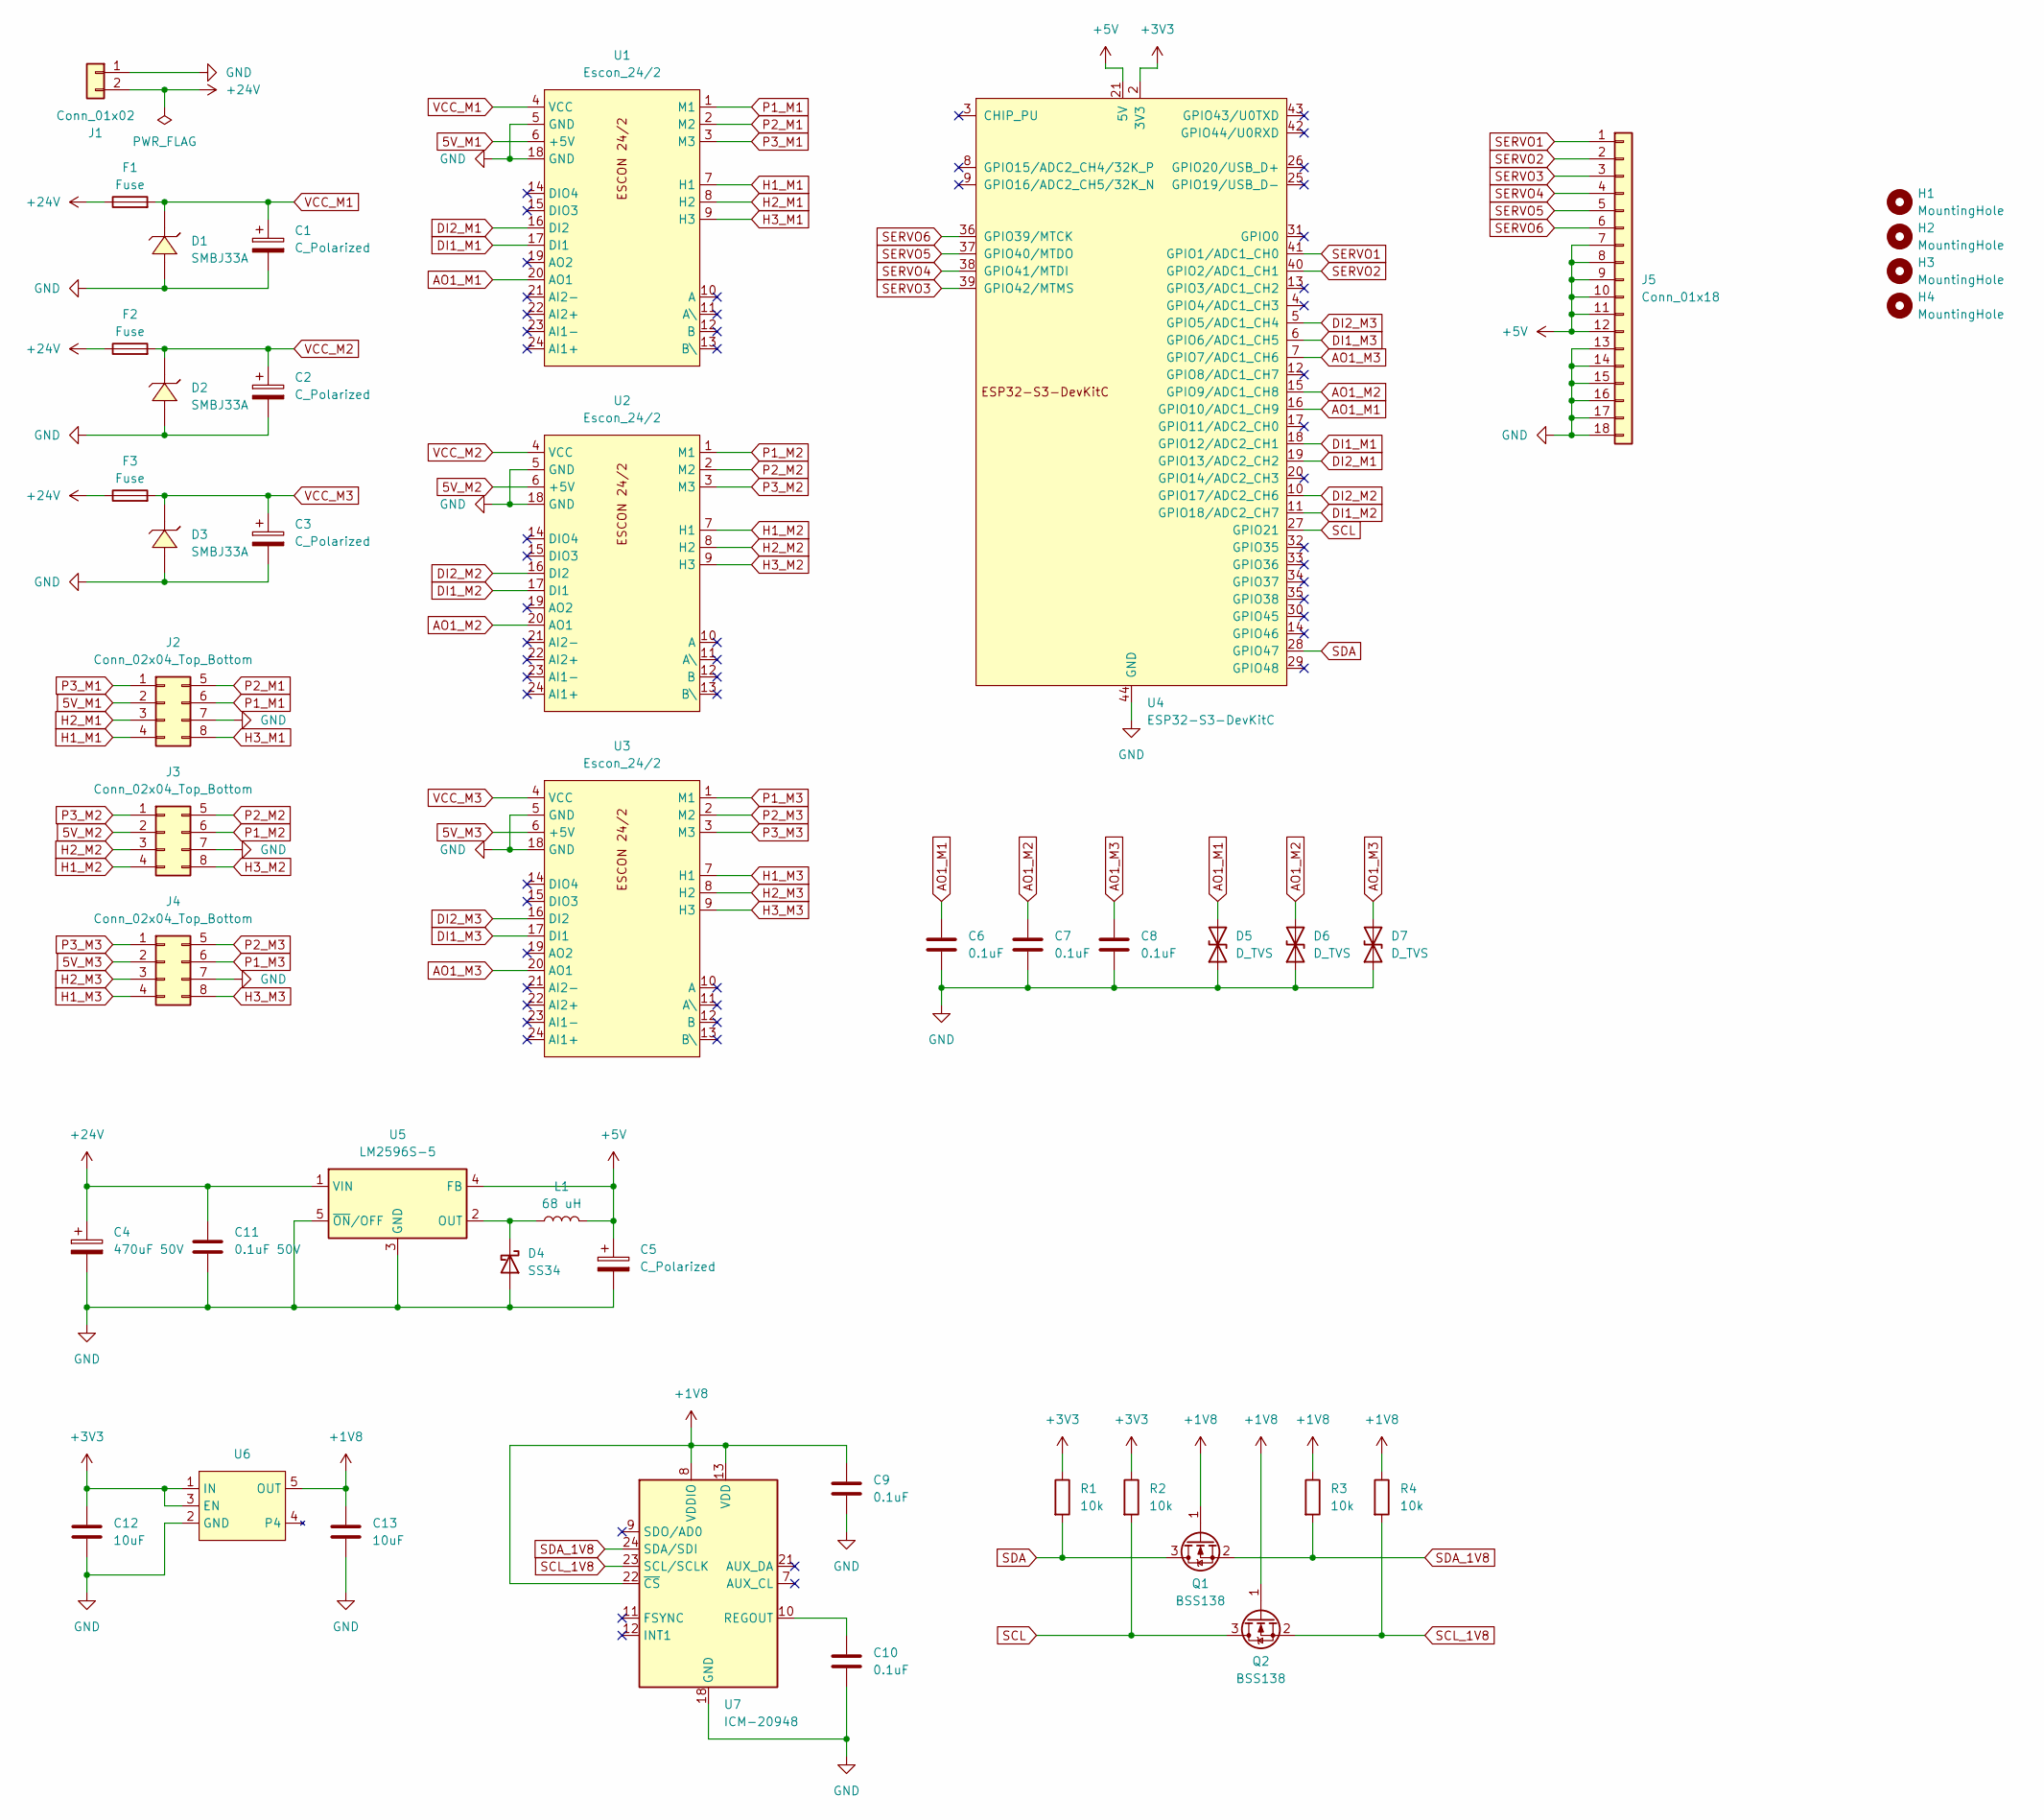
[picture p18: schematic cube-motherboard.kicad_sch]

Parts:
C1, C2, C3: C_Polarized; CP_Radial_D12.5mm_P5.00mm
C4: 470uF 50V; CP_Radial_D18.0mm_P7.50mm
C5: C_Polarized; CP_Radial_D10.0mm_P5.00mm
C6, C7, C8, C9, C10: 0.1uF; C_0603_1608Metric
C11: 0.1uF 50V; C_0603_1608Metric
C12, C13: 10uF; C_0603_1608Metric
D1, D2, D3: SMBJ33A; SMB_L4.4-W3.6-LS5.4-RD
D4: SS34; D_SOD-123F
D5, D6, D7: D_TVS; D_0402_1005Metric
F1, F2, F3: Fuse; Littelfuse 0157004.DR
H1, H2, H3, H4: MountingHole; MountingHole_3.2mm_M3_DIN965_Pad
J1: Conn_01x02; AMASS_XT60-F_1x02_P7.20mm_Vertical
J2, J3, J4: Conn_02x04_Top_Bottom; Molex_Mini-Fit_Jr_5566-08A_2x04_P4.20mm_Vertical
J5: Conn_01x18; PinHeader_03x06
L1: 68 uH; Bourns SRP1050WA-680M
Q1, Q2: BSS138; SOT-23
R1, R2, R3, R4: 10k; R_0603_1608Metric
U1, U2, U3: Escon_24/2; Escon_24
U4: ESP32-S3-DevKitC
U5: LM2596S-5; TO-263-5_TabPin3
U6: SOT-23-5
U7: ICM-20948; InvenSense_QFN-24_3x3mm_P0.4mm

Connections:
5V_M1: J2.2, U1.6 (+5V)
5V_M2: J3.2, U2.6 (+5V)
5V_M3: J4.2, U3.6 (+5V)
+1V8: C9.1, C13.1, Q1.1 (G), Q2.1 (G), R3.1, R4.1, U6.5 (OUT), U7.8 (VDDIO), U7.13 (VDD), U7.22 (~CS)
+3V3: C12.1, R1.1, R2.1, U4.1 (3V3), U4.2 (3V3), U6.1 (IN), U6.3 (EN)
+5V: C5.1, J5.7, J5.8, J5.9, J5.10, J5.11, J5.12, L1.2, U4.21 (5V), U5.4 (FB)
+24V: C4.1, C11.1, F1.1, F2.1, F3.1, J1.2, U5.1 (VIN)
AO1_M1: C6.1, D5.2 (A2), U1.20 (AO1), U4.16 (GPIO10/ADC1_CH9)
AO1_M2: C7.1, D6.2 (A2), U2.20 (AO1), U4.15 (GPIO9/ADC1_CH8)
AO1_M3: C8.1, D7.2 (A2), U3.20 (AO1), U4.7 (GPIO7/ADC1_CH6)
DI1_M1: U1.17 (DI1), U4.18 (GPIO12/ADC2_CH1)
DI1_M2: U2.17 (DI1), U4.11 (GPIO18/ADC2_CH7)
DI1_M3: U3.17 (DI1), U4.6 (GPIO6/ADC1_CH5)
DI2_M1: U1.16 (DI2), U4.19 (GPIO13/ADC2_CH2)
DI2_M2: U2.16 (DI2), U4.10 (GPIO17/ADC2_CH6)
DI2_M3: U3.16 (DI2), U4.5 (GPIO5/ADC1_CH4)
GND: C1.2, C2.2, C3.2, C4.2, C5.2, C6.2, C7.2, C8.2, C9.2, C10.2, C11.2, C12.2, C13.2, D1.2 (A), D2.2 (A), D3.2 (A), D4.2 (A), D5.1 (A1), D6.1 (A1), D7.1 (A1), J1.1, J2.7, J3.7, J4.7, J5.13, J5.14, J5.15, J5.16, J5.17, J5.18, U1.5 (GND), U1.18 (GND), U2.5 (GND), U2.18 (GND), U3.5 (GND), U3.18 (GND), U4.22 (GND), U4.23 (GND), U4.24 (GND), U4.44 (GND), U5.3 (GND), U5.5 (~ON/OFF), U6.2 (GND), U7.18 (GND), U7.20 (GND)
H1_M1: J2.4, U1.7 (H1)
H1_M2: J3.4, U2.7 (H1)
H1_M3: J4.4, U3.7 (H1)
H2_M1: J2.3, U1.8 (H2)
H2_M2: J3.3, U2.8 (H2)
H2_M3: J4.3, U3.8 (H2)
H3_M1: J2.8, U1.9 (H3)
H3_M2: J3.8, U2.9 (H3)
H3_M3: J4.8, U3.9 (H3)
unnamed: D4.1 (K), L1.1, U5.2 (OUT)
unnamed: C10.1, U7.10 (REGOUT)
P1_M1: J2.6, U1.1 (M1)
P1_M2: J3.6, U2.1 (M1)
P1_M3: J4.6, U3.1 (M1)
P2_M1: J2.5, U1.2 (M2)
P2_M2: J3.5, U2.2 (M2)
P2_M3: J4.5, U3.2 (M2)
P3_M1: J2.1, U1.3 (M3)
P3_M2: J3.1, U2.3 (M3)
P3_M3: J4.1, U3.3 (M3)
SCL: Q2.3 (D), R2.2, U4.27 (GPIO21)
SCL_1V8: Q2.2 (S), R4.2, U7.23 (SCL/SCLK)
SDA: Q1.3 (D), R1.2, U4.28 (GPIO47)
SDA_1V8: Q1.2 (S), R3.2, U7.24 (SDA/SDI)
SERVO1: J5.1, U4.41 (GPIO1/ADC1_CH0)
SERVO2: J5.2, U4.40 (GPIO2/ADC1_CH1)
SERVO3: J5.3, U4.39 (GPIO42/MTMS)
SERVO4: J5.4, U4.38 (GPIO41/MTDI)
SERVO5: J5.5, U4.37 (GPIO40/MTDO)
SERVO6: J5.6, U4.36 (GPIO39/MTCK)
VCC_M1: C1.1, D1.1 (C), F1.2, U1.4 (VCC)
VCC_M2: C2.1, D2.1 (C), F2.2, U2.4 (VCC)
VCC_M3: C3.1, D3.1 (C), F3.2, U3.4 (VCC)

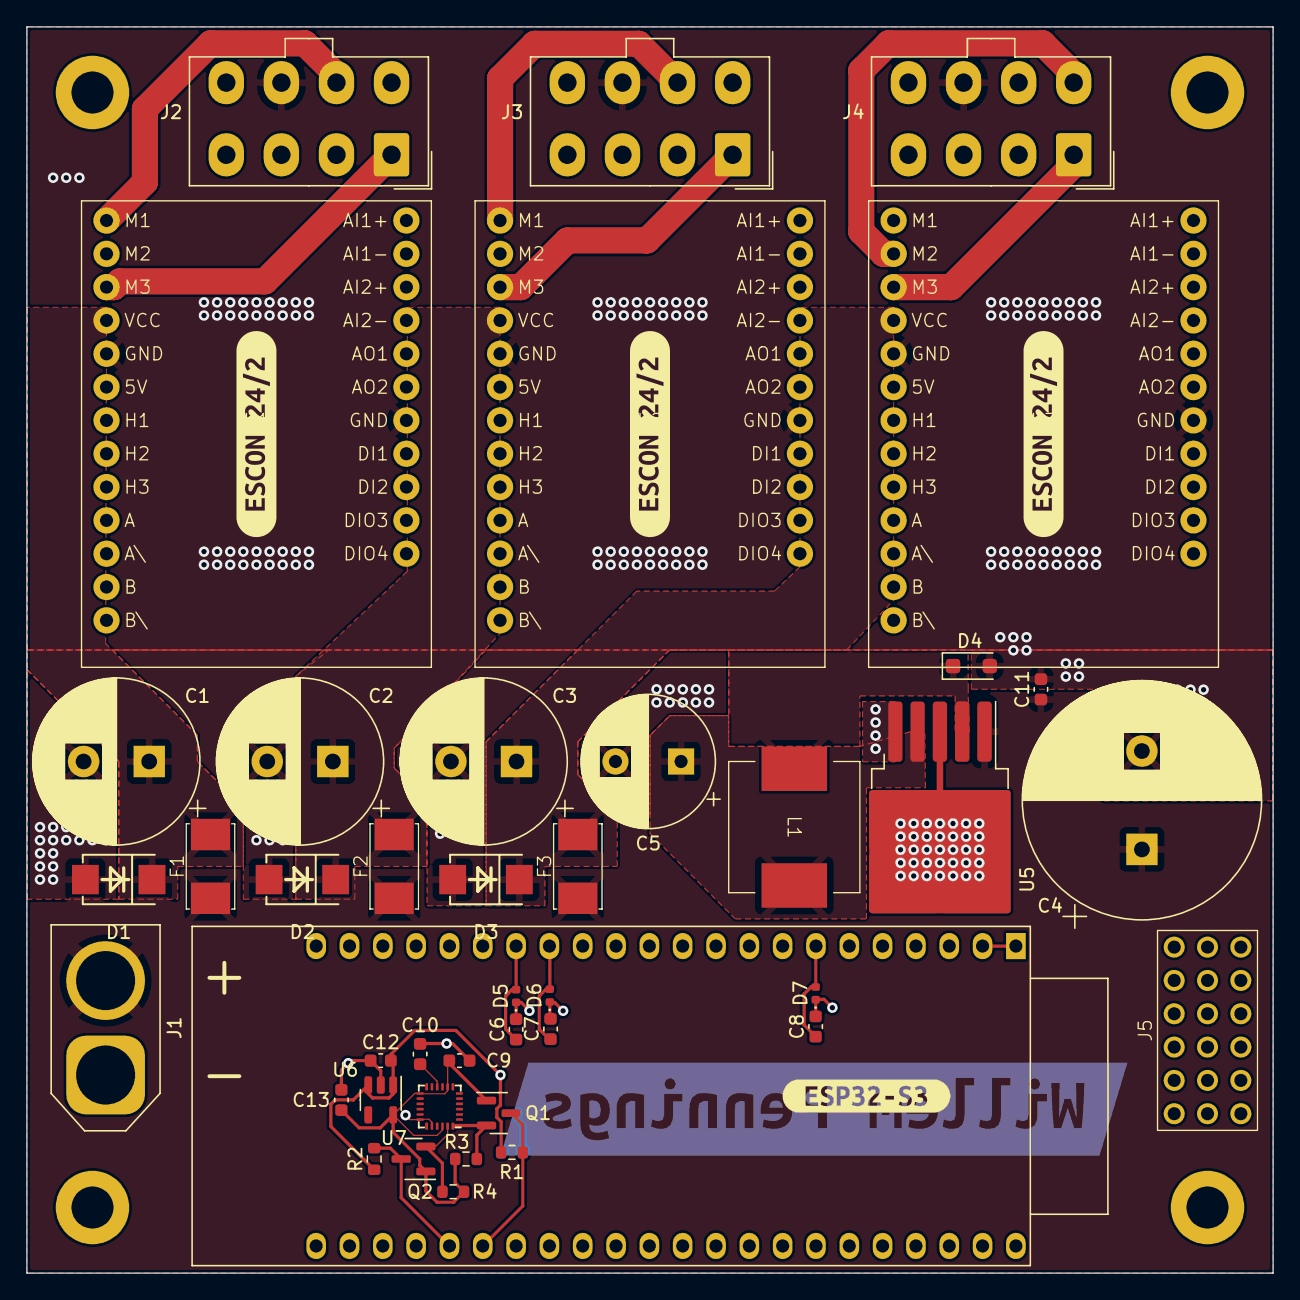
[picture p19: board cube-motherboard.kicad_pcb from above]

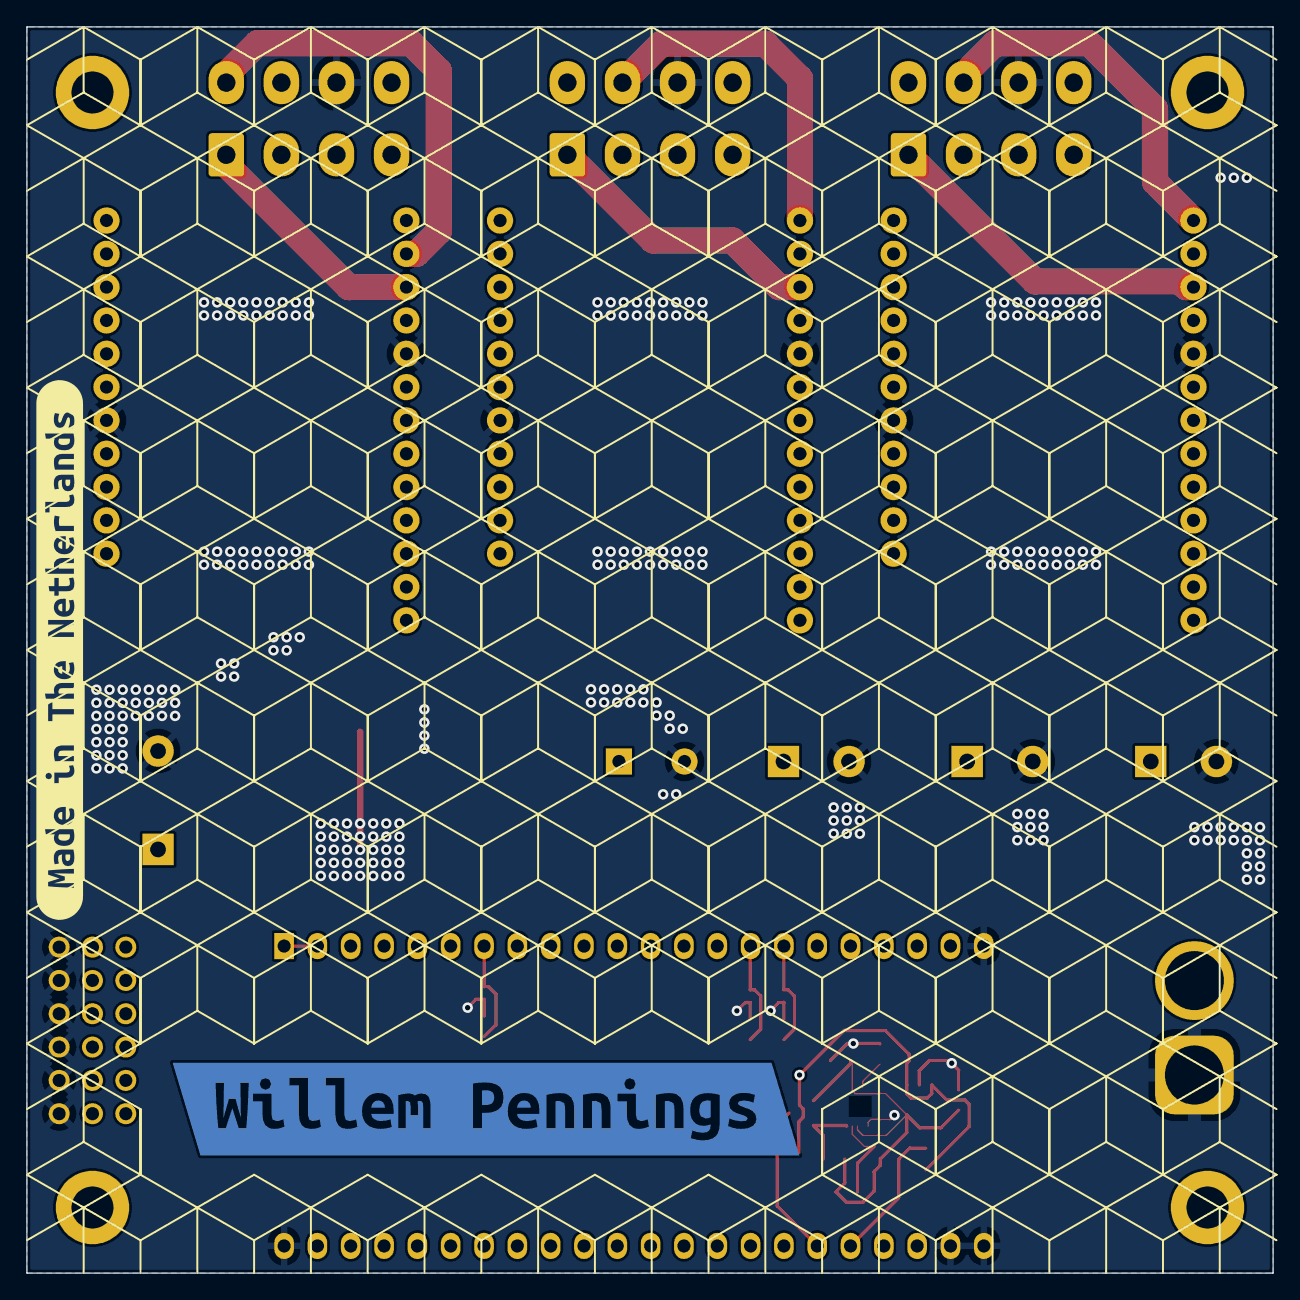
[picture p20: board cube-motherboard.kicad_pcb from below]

Board: 4 copper layers, 95.0 x 95.0 mm, 52 parts (2 on the bottom side), 50 nets.

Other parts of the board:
kibuzzard-65625AD1: G***; kibuzzard-65625AD1
kibuzzard-65625B38: G***; kibuzzard-65625B38
kibuzzard-65625B53, kibuzzard-65625B53#2, kibuzzard-65625B53#3: G***; kibuzzard-65625B53
kibuzzard-656267AE: G***; kibuzzard-656267AE

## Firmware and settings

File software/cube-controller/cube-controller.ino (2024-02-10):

// Toggle over-the-air (WiFi) programming functionality (0 = disabled, 1 = enabled)
#define OTA 1

// Toggle between use of nonlinear or linear controller (0 = linear, 1 = nonlinear)
#define USE_NONLINEAR_CONTROLLER 1

// TickTwo provides ESP32-compatible timers
#include <TickTwo.h>

#if OTA
  // Libraries related to wireless functionality
  #include <WiFi.h>
  #include <ESPmDNS.h>
  #include <WiFiUdp.h>
  #include <ArduinoOTA.h>
#endif

// Cube controller library
#include "src/cube-controller.h"

#if OTA
  // WiFi settings
  const char* wifi_ssid = "YOUR_SSID";
  const char* wifi_password = "YOUR_PASSWORD";
#endif

// Instantiation of objects
Motor motor1(M1_ENABLE, M1_CURRENT), motor2(M2_ENABLE, M2_CURRENT), motor3(M3_ENABLE, M3_CURRENT);
WheelEstimator whe_est_1(M1_SPEED), whe_est_2(M2_SPEED), whe_est_3(M3_SPEED);
AttitudeEstimator att_est(IMU_SDA, IMU_SCL);
AttitudeWheelController cont(USE_NONLINEAR_CONTROLLER);
AttitudeTrajectory att_tra;

// Run cube controller at the frequency as specified in parameter file
void controller();
TickTwo timer(controller, dt_us, 0, MICROS_MICROS);

// Status LED control: LED is either solid or blinking at 2.5 Hz
void control_led();
TickTwo timer_led(control_led, 200, 0, MILLIS);

#if OTA
  // Handle OTA flashing requests every 5 seconds
  void handle_ota();
  TickTwo timer_ota(handle_ota, 5000, 0, MILLIS);
#endif

// Quaternion and angle error
float qe0, qe1, qe2, qe3;
float phi;
float phi_lim = phi_min;

// Trajectory initialization flag
bool flag_tra = false;

// LED status when blinking
bool led_status = false;

// Security flags
bool flag_arm = false;
bool flag_terminate = false;

// Torques
float tau_1 = 0, tau_2 = 0, tau_3 = 0;

void setup() {
  // Open serial connection
  Serial.begin(921600);
  Serial.println("This is the ESP32 cube controller.");

  #if OTA
    // Set up WiFi connection
    WiFi.mode(WIFI_STA);
    WiFi.begin(wifi_ssid, wifi_password);

    unsigned int nAttempts = 0;
    while (WiFi.waitForConnectResult() != WL_CONNECTED && nAttempts < 3) {
      delay(1000);
      nAttempts++;
    }

    // If WiFi connection failed, indicate this using six yellow flashes
    if(WiFi.waitForConnectResult() != WL_CONNECTED) {
      for(int i = 0; i < 5; i++) {
        neopixelWrite(RGB_BUILTIN, 255, 255, 0);
        delay(250);
        neopixelWrite(RGB_BUILTIN, 0, 0, 0);
        delay(250);
      }
    }

    // Set hostname
    ArduinoOTA.setHostname("Cube ESP32");

    // Print WiFi status
    Serial.print("Connected to WiFi (local IP is ");
    Serial.print(WiFi.localIP());
    Serial.println(").");

    // Set up OTA flashing using ArduinoOTA
    ArduinoOTA.begin();
  #endif

  // Delay for one second to allow Maxon ESCON drivers to fully initialize
  delay(1000);

  // Motor setup (also spins each motor in positive direction very briefly)
  motor1.init();
  motor2.init();
  motor3.init();

  // Wheel estimator initialization (also calibrates the hall sensor for each wheel)
  whe_est_1.init();
  whe_est_2.init();
  whe_est_3.init();

  // Attitude estimator initialization (also calibrates the gyroscope)
  att_est.init();

  // Start controller and LED timers
  timer.start();
  timer_led.start();

  #if OTA
    // OTA handler timer
    timer_ota.start();
  #endif
}

void loop() {
  // Update controller timer
  timer.update();
  timer_led.update();

  #if OTA
    // Handle OTA updates
    timer_ota.update();
  #endif
}

#if OTA
  void handle_ota(){
    ArduinoOTA.handle();
  }
#endif

void controller() {
  // Estimate wheel velocities
  whe_est_1.estimate(tau_1);
  whe_est_2.estimate(tau_2);
  whe_est_3.estimate(tau_3);

  // Estimate cube attitude
  att_est.estimate();

  // Calculate rotation quaternion error
  qe0 = att_est.q0 * att_tra.qr0 + att_est.q1 * att_tra.qr1 + att_est.q2 * att_tra.qr2 + att_est.q3 * att_tra.qr3;
  qe1 = att_est.q0 * att_tra.qr1 - att_est.q1 * att_tra.qr0 - att_est.q2 * att_tra.qr3 + att_est.q3 * att_tra.qr2;
  qe2 = att_est.q0 * att_tra.qr2 - att_est.q2 * att_tra.qr0 + att_est.q1 * att_tra.qr3 - att_est.q3 * att_tra.qr1;
  qe3 = att_est.q0 * att_tra.qr3 - att_est.q1 * att_tra.qr2 + att_est.q2 * att_tra.qr1 - att_est.q3 * att_tra.qr0;

  // Normalize rotation quaternion error (real part only since we don't need the rest)
  qe0 /= sqrt(qe0 * qe0 + qe1 * qe1 + qe2 * qe2 + qe3 * qe3);

  // Calculate error angle
  phi = 2.0 * acos(qe0);

  // Controller enable and disable logic. The controller only activates once its orientation is such that the error with
  // respect to the desired orientation is smaller than phi_min. As soon as this is reached, the error tolerance phi_lim
  // is increased to phi_max. If this error is exceeded, the controller is disabled until the chip is reset.
  if(abs(phi) <= phi_lim && !flag_terminate) {
    // Controller is active
    flag_arm = true;

    // Increase error range to the maximum limit
    phi_lim = phi_max;

    // Generate trajectory
    // Comment out the generate() method if the cube is balancing on a side instead of a corner
    if(!flag_tra) {
      flag_tra = true;
      att_tra.init();
    }
    att_tra.generate();

    // Controller calculates motor torques based on cube and wheel states
    cont.control(att_tra.qr0, att_tra.qr1, att_tra.qr2, att_tra.qr3, att_est.q0, att_est.q1, att_est.q2, att_est.q3,
      att_tra.omega_r_x, att_tra.omega_r_y, att_tra.omega_r_z, att_est.omega_x, att_est.omega_y, att_est.omega_z, 
      att_tra.alpha_r_x, att_tra.alpha_r_y, att_tra.alpha_r_z, whe_est_1.theta_w, whe_est_2.theta_w, 
      whe_est_3.theta_w, whe_est_1.omega_w, whe_est_2.omega_w, whe_est_3.omega_w);

    // Get motor torques from controller
    tau_1 = cont.tau_1;
    tau_2 = cont.tau_2;
    tau_3 = cont.tau_3;
  } else {
    // Outside safe limits: reset motor torques to zero
    tau_1 = 0.0;
    tau_2 = 0.0;
    tau_3 = 0.0;

    // Disarm mechanism
    if(flag_arm) {
      flag_arm = false;
      flag_terminate = true;
    }
  }

  // Apply torques to motors
  // When balancing on the x side, comment out motor 2 and 3. When balancing on the y side, comment out 1 and 3.
  motor1.set_torque(tau_1);
  motor2.set_torque(tau_2);
  motor3.set_torque(tau_3);
}

void control_led() {
  if(flag_arm) {
    if(abs(phi) <= phi_lim - 10 * pi / 180) {
      // Cube is not close to error limit: solid green LED
      neopixelWrite(RGB_BUILTIN, 0, 255, 0);
    } else {
      // Cube is close to error limit: alternate between red and green. Cube should be manually put to rest.
      if(led_status) {
        neopixelWrite(RGB_BUILTIN, 255, 0, 0);
      } else {
        neopixelWrite(RGB_BUILTIN, 0, 255, 0);
      }
      led_status = !led_status;
    }
  } else {
    if(flag_tra) {
      // A trajectory was already generated so the cube must now be halted due to a limit error
      if(led_status) {
        neopixelWrite(RGB_BUILTIN, 0, 0, 0);
      } else {
        neopixelWrite(RGB_BUILTIN, 255, 0, 0);
      }
      led_status = !led_status;
    } else {
      // Show a solid red LED to indicate readiness to start
      neopixelWrite(RGB_BUILTIN, 255, 0, 0);
    }
  }
}

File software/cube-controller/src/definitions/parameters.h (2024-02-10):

#ifndef parameters_h
#define parameters_h

// System frequencies and periods
const float f = 250;
const float dt = 1 / f;
const unsigned int dt_us = dt * 1e6;

// IMU gyroscope offsets
const float b_gyr_x = 0.74;
const float b_gyr_y = 0.66;
const float b_gyr_z = -0.45;

// IMU accelerator offsets and gains
const float b_acc_x = -6;
const float b_acc_y = -215;
const float b_acc_z = 161;
const float f_acc_x = 1672.7;
const float f_acc_y = 1673.3;
const float f_acc_z = 1691.5;

// Physical parameters
const float pi = 3.14159265359;
const float g = 9.80665;

// Surface parameters
const float b = 0.0;

// Electrical motor properties
const float Ra = 0.942; // Armature (winding) resistance (Ohm)
const float La = 0.363e-3; // Armature (winding) inductance (H)
const float Km = 36e-3; // Torque constant (Nm/A)
const float ia_max = 6; // Maximum current (A)
const float omega_nl = 6250 * pi / 30; // No load speed (rad/s)

// Mechanical motor properties
const float tau_c = 3.4e-3; // Coulomb friction torque (Nm)
const float bw = 1.513e-5; // Rotational viscous friction coefficient (Nms/rad)

// Structure properties
const float l = 0.15; // Structure side length (m)
const float m_s = 1.0; // Structure mass (kg)
const float I_s_xx = 3e-3; // Structure moment of inertia around xyz at center of mass (kgm^2)

// Reaction wheel properties
const float m_w = 0.225; // Reaction wheel mass (kg)
const float I_w_xx = 4.855e-4; // Reaction wheel moment of inertia around x axis at center of mass (kgm^2)
const float I_w_yy = 2.439e-4; // Reaction wheel moment of inertia around yz axis at center of mass (kgm^2)

// Combined properties of structure and reaction wheels
const float m_c = m_s + 3 * m_w; // Cubli total mass (kg)
const float I_c_xx_bar = I_s_xx + 2 * I_w_yy + (m_s + 2.0 * m_w) * l * l / 2.0; // In-plane moment of inertia (kgm^2)
const float I_c_xy_bar = -(m_s + m_w) * l * l / 4.0; // Out-of-plane moment of inertia (kgm^2)

// Auxiliary parameters
const float m_c_bar = m_c - m_w;
const float m_c_bar_g_l = m_c_bar * g * l;

// Estimator gains
const float lds = 1; // How much do you trust the accelerometer compared to the gyroscope? This gain determines that.
const float ldw = 150; // How much do you trust the hall sensor compared to the wheel model? This gain determines that.

// Controller gains. These must be re-tuned if your cube has different dynamics (weights, inertias, dimensions, etc.)
const float kp = 300;
const float kd = 40;
const float kpw = 0.009;
const float kdw = 0.02;

// One out of three of the following initial reference quaternions should be uncommented
// Quaternion reference (Cubli sitting on on corner, corrected for center of mass misalignment)
const float phi_e = 0 * pi / 180.0;
const float qu0 =                    cos(phi_e / 2.0 + acos(sqrt(3.0) / 3.0) / 2.0);
const float qu1 =  sqrt(2.0) / 2.0 * sin(phi_e / 2.0 + acos(sqrt(3.0) / 3.0) / 2.0);
const float qu2 = -sqrt(2.0) / 2.0 * sin(phi_e / 2.0 + acos(sqrt(3.0) / 3.0) / 2.0);
const float qu3 =  0.0;

// Quaternion reference (Cubli sitting on x axis edge, corrected for center of mass misalignment)
// const float phi_e = -3.0 * pi / 180.0;
// const float qu0 = cos(phi_e / 2.0 - pi / 8.0);
// const float qu1 = cos(phi_e / 2.0 + 3.0 * pi / 8.0);
// const float qu2 = 0.0;
// const float qu3 = 0.0;

// Quaternion reference (Cubli sitting on y axis edge, corrected for center of mass misalignment)
// const float phi_e = -3.0 * pi / 180.0;
// const float qu0 = cos(phi_e / 2.0 - pi / 8.0);
// const float qu1 = 0.0;
// const float qu2 = -cos(phi_e / 2.0 + 3.0 * pi / 8.0);
// const float qu3 = 0.0;

// Quaternion stuff
const float qu0_qu0 = qu0 * qu0;
const float qu0_qu1 = qu0 * qu1;
const float qu0_qu2 = qu0 * qu2;
const float qu0_qu3 = qu0 * qu3;
const float qu1_qu1 = qu1 * qu1;
const float qu1_qu2 = qu1 * qu2;
const float qu1_qu3 = qu1 * qu3;
const float qu2_qu2 = qu2 * qu2;
const float qu2_qu3 = qu2 * qu3;
const float qu3_qu3 = qu3 * qu3;

// Minimum and maximum error limits (for control safety)
const float phi_min = 5.0 * pi / 180.0;
const float phi_max = 40.0 * pi / 180.0;

// Minimum jerk trajectory parameters
const float pos_traj = 2.0 * pi; // Trajectory path (rad)
const float t_rest = 10.0; // Rest time (s)
const float t_traj = 20.0; // Trajectory time (s)
const float cra_0 = 720.0 * pos_traj / pow(t_traj, 5);
const float sna_0 = 360.0 * pos_traj / pow(t_traj, 4);
const float jer_0 =  60.0 * pos_traj / pow(t_traj, 3);

#endif

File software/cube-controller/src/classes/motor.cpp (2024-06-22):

#include "motor.h"

// Class constructor
Motor::Motor(int pin_enable, int pin_current) : pin_enable(pin_enable), pin_current(pin_current) {
    // Configure enable pin as digital output
    pinMode(pin_enable, OUTPUT);

    // Map pin number to channel (these must be updated if mx_current in pins.h is changed...)
    if(pin_current == 12) {
        channel = 0;
    } else if(pin_current == 18) {
        channel = 1;
    } else {
        channel = 2;
    }

    // Configure current pin as 1 kHz 12-bit PWM output
    ledcSetup(channel, 1000, 12);
    ledcAttachPin(pin_current, channel);
}

void Motor::init() {
    // Briefly set current to verify motor behaviour
    set_current(0.5);
    delay(250);
    set_current(-0.4);
    delay(250);
    set_current(0);
}

void Motor::set_current(float ia) {
    // Variables
    bool enable;
    float current;

    // Reverse motor current because of definitions (positive corresponds to CCW rotation)
    ia = -ia;

    if (ia == 0.0) {
        // If current is zero, disable motor and set corresponding PWM value
        enable = false;
        current = 0.5;   
    } else {
        // Enable motor
        enable = true;

        // Set PWM value according to current input. Upper and lower 10% are not used for reliability. ESCON drivers are
        // configured accordingly.
        if(ia > ia_max) {
            // Saturation at upper limit
            current = 0.9;
        } else if (ia < -ia_max) {
            // Saturation at lower limit
            current = 0.1;
        } else {
            // Interpolation in valid range
            current = 0.5 + ia * (0.8 / (2.0 * ia_max));
        }
    }

    // Set enable pin
    digitalWrite(pin_enable, enable);

    // Map 0-1 PWM value to 12-bit range (0-4095) and write duty
    uint32_t duty = current * 4095;
    ledcWrite(channel, duty);
}

void Motor::set_torque(float tau) {
    // Convert torque to current using motor torque constant Km
    set_current(tau / Km);
}

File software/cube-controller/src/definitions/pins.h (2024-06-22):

#ifndef pins_h
#define pins_h

// Motor controllers
const int M1_ENABLE = 13;
const int M1_CURRENT = 12;
const int M2_ENABLE = 17;
const int M2_CURRENT = 18;
const int M3_ENABLE = 5;
const int M3_CURRENT = 6;

// Motor speeds
const int M1_SPEED = 10;
const int M2_SPEED = 9;
const int M3_SPEED = 7;

// IMU
const int IMU_SDA = 47;
const int IMU_SCL = 21;

#endif

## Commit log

2024-02-10 Publish files
    [3x6 Male Pin Header.STEP, 466023_escon_module_24-2.stp, L201011MS02Q.stp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]
2024-02-21 Add bearings to BOM
    [bom.xlsx]
2024-05-29 Fix unconnected GND circuit for J2 (pin 1)
    [cube-batteryboard.kicad_pcb, cube-batteryboard.kicad_sch]
2024-06-20 Organize esp32 <-> escon wiring
    Remapped AO1 of M3 to an ADC1 pin.
    Removed all three unused AO2 DI3 wirings and relevant diodes and capacitors
    Corrected pins.h (Old version was not matching with old schematic btw)
    Updated Bom accordingly
    [bom.xlsx, cube-motherboard.kicad_pcb, cube-motherboard.kicad_sch]
2024-06-20 Fix symbol, footprint and orientation of D1,D2 and D3 diodes
    Add missing 3D models for L1 & F1,F2,F3
    [0157004.DRT.STEP, IND_SRP1050_BRN.step, SMB_L4.4-W3.6-LS5.4-RD.step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]
2024-06-20 fix labels for on off switch
    [cube-batteryboard.kicad_pcb]
2024-06-21 Remove the requirement to remap the pins of the molex cables by reorganizing pin order
    [cube-motherboard.kicad_pcb, cube-motherboard.kicad_sch]

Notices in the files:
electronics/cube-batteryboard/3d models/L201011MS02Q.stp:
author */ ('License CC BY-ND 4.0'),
